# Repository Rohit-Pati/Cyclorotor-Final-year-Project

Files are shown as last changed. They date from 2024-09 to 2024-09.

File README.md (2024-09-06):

## Cyclorotor

Cyclorotor, also known as cycloidal rotor or cyclogiro, is a type of propulsion system which converts shaft power into the acceleration of fluid using a rotating axis parallel to the blade span (alternatively, rotating axis perpendicular to the direction of fluid motion). It consists of several blades around the axis of rotation with spanwise axis parallel to the axis of rotation. These blades are cyclically pitched twice per revolution implementing the control mechanism of Voith Schneider propeller to produce thrust in any direction normal to the axis of rotation.

This project was developed as part of the requirements for a bachelor's degree with the objective of experimentally observing the thrust pattern. A well-functioning four blades cyclorotor was manufactured using design parameters inferred and derived from various published articles.

## Design Specifications

Airfoil                                      : NACA0015

Chord Length                                 : 50.8 mm

Blade Span                                   : 171 mm

Blade distance offset from axis of rotation  : 3 inch (152.4 mm)

Pitching axis point                          : 25% of chord from leading edge

Control(actuation) point in airfoil          : 17.5 mm

Length of control rods                       : 76.2 mm

## Power System Specifications

Motor Specification  : 1400 KV

Driver Pulley        : GT2 Timing Pulley 20 Teeth with 5 mm bore

Driven Pulley        : GT2 Timing Pulley 60 Teeth

Pulley Belt          : GT2 Timing Pulley 200mm

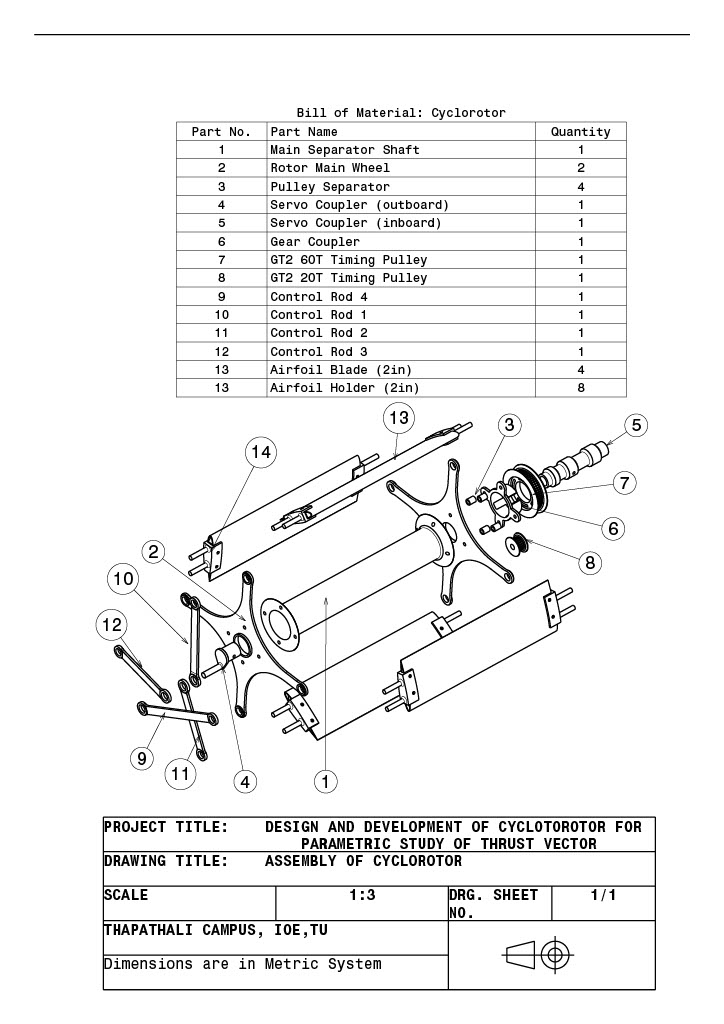
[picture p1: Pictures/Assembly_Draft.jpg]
Assembly


Here are some pictures of final product after manufacture and assembly.

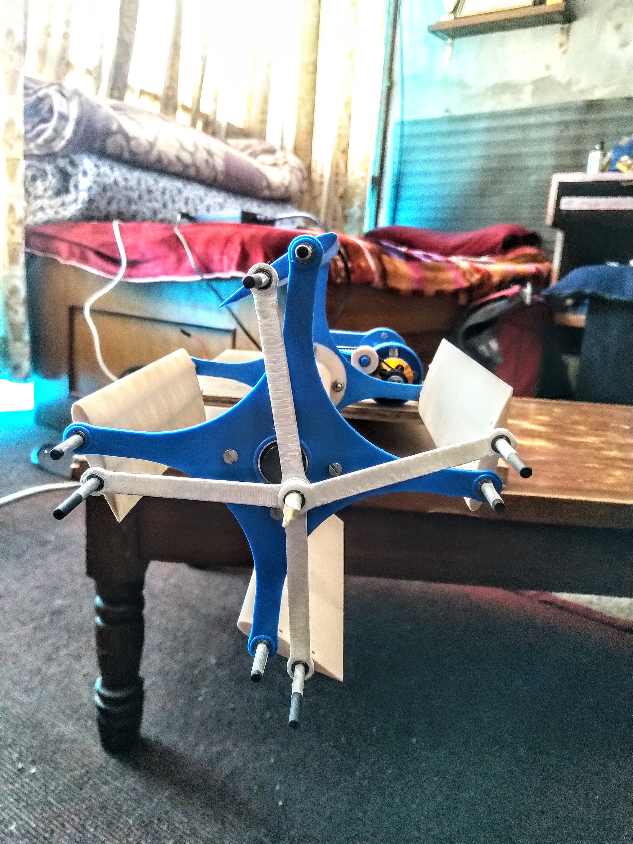
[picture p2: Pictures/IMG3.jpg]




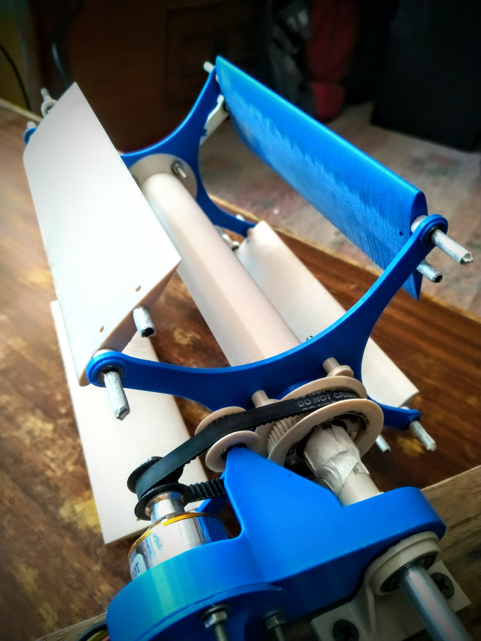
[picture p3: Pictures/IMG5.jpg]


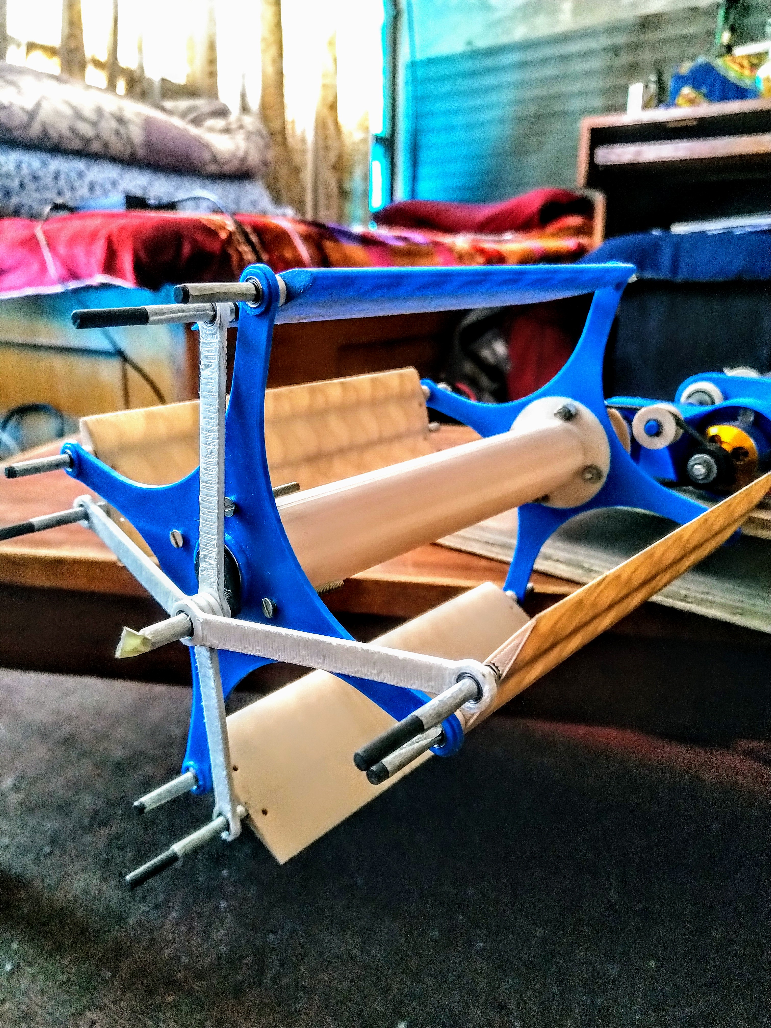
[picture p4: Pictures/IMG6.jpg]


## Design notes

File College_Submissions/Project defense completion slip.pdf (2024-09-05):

Department of Automobile and Mechanical Engineering FYP REPORT NO: 010

Batch: 2075 | Program: Bachelor’s in mechanical engineering (BME)

Final Year Title: DESIGN AND DEVELOPMENT OF CYCLOROTOR FOR PARAMETRIC

STUDY OF THRUST VECTORING

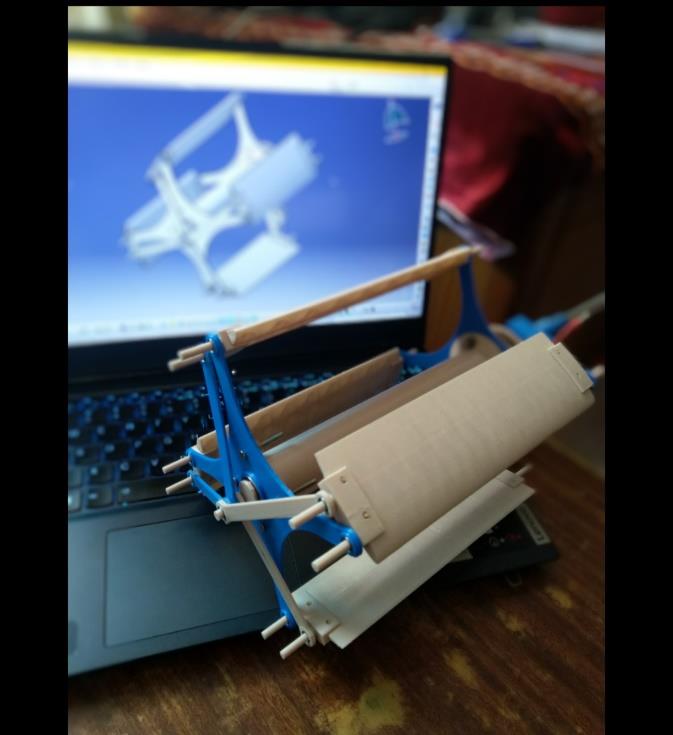
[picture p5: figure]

Student Name list/CRN:

Abhishek Kandel (THA075BME003)

Milan Dhami (THA075BME019)

Ringjing Tamang (THA075BME030)

Rohit Pati | (THA075BME031)

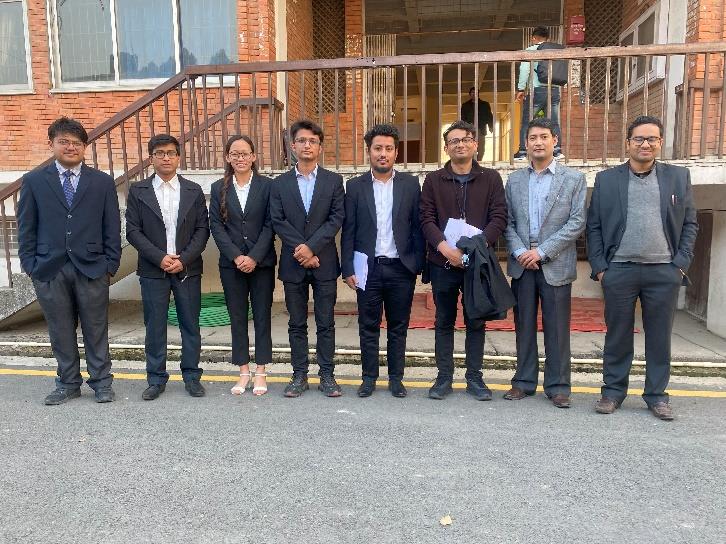
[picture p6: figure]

Contact:

abhisekrishi123@gmail.com

milandhami004@gmail.com

tamangrj22@gmail.com

rohit.075bme031@tcioe.edu.np

Supervisor:

Er.Biman Rimal

Abstract:

Cyclorotor is a horizontal axis propulsion system with airfoil blades attached between two rotor wheels parallelly to the axis of rotation. The unique feature of this propulsion system is the variable pitching mechanism which offers better maneuverability characteristic for air vehicles. This propulsion system is claimed to produce adequate thrust even at low speed which helps to simplify the rotating mechanism and reduce noise which has widened its scope for use in VTOL aircraft. Research has been going on in this field with the quest of optimizing it for use in air vehicles. It is important to have a better control system for propulsion systems and aircraft to acquire airworthiness. For a better control system of the variable pitching mechanism in a cyclorotor, it is required to have knowledge on the thrust vector pattern. Hence this report discusses the experimental study of thrust vector in cyclorotor where the thrust vector pattern is analyzed with respect to the eccentricity phase angle.

Department of Automobile and Mechanical Engineering FYP REPORT NO: 010

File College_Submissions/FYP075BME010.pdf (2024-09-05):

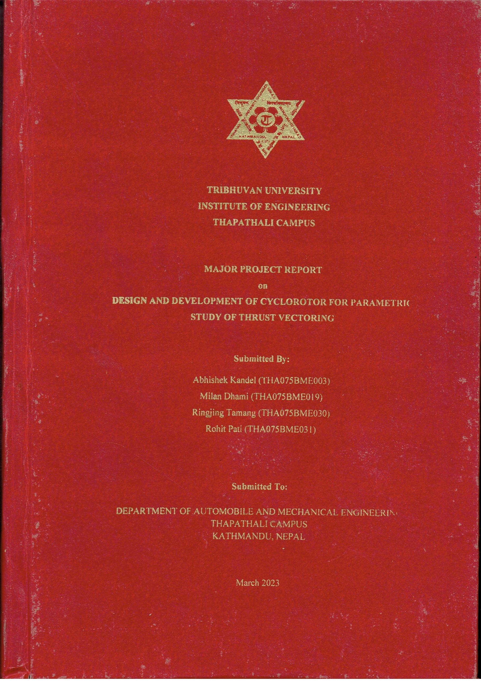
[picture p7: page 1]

TRIBHUVAN UNIVERSITY

INSTITUTE OF ENGINEERING

THAPATHALI CAMPUS

MAJOR PROJECT REPORT

on

DESIGN AND DEVELOPMENT OF CYCLOROTOR FOR PARAMETRIC

STUDY OF THRUST VECTORING

Submitted By:

Abhishek Kandel (THA075BME003)

Milan Dhami (THA075BME019)

Ringjing Tamang (THA075BME030)

Rohit Pati (THA075BME031)

Submitted To:

DEPARTMENT OF AUTOMOBILE AND MECHANICAL ENGINEERING THAPATHALI CAMPUS
KATHMANDU, NEPAL

March 2023

TRIBHUVAN UNIVERSITY

INSTITUTE OF ENGINEERING

THAPATHALI CAMPUS

MAJOR PROJECT REPORT

on

DESIGN AND DEVELOPMENT OF CYCLOROTOR FOR PARAMETRIC

STUDY OF THRUST VECTORING

Submitted By:

Abhishek Kandel (THA075BME003)

Milan Dhami (THA075BME019)

Ringjing Tamang (THA075BME030)

Rohit Pati (THA075BME031)

Submitted To:

DEPARTMENT OF AUTOMOBILE AND MECHANICAL ENGINEERING THAPATHALI CAMPUS, KATHMANDU, NEPAL

In the partial fulfillment of the award of the Bachelor’s Degree in Mechanical

Engineering

Under the Supervision of

Er. Biman Rimal

March 2023

ii

COPYRIGHT

The author has agreed that the library, Department of Automobile and Mechanical

Engineering, Thapathali Campus, Institute of Engineering may make this project report

freely available for inspection and study. Moreover, the author has agreed that

permission for extensive copying of this project report for scholarly purposes may be

granted by the professor who supervised the project work recorded herein or, in their

absence, by the Head of the Department wherein the project report was done. It is

understood that recognition will be given to the author of this report and to the

Department of Automobile and Mechanical Engineering, Thapathali Campus, Institute

of Engineering, in any use of the material of this project report.

Copying or publication or other illegal and immoral use of this report for financial gain

without the approval of the Department of Automobile and Mechanical Engineering,

Thapathali Campus Institute of Engineering and author’s written permission is strictly

prohibited.

Request for permission to copy or to make any other use of the material in this report,

in whole or in part, should be addressed to:

Head

Department of Automobile and Mechanical Engineering

Thapathali Campus, Institute of Engineering

Thapathali, Kathmandu

Nepal

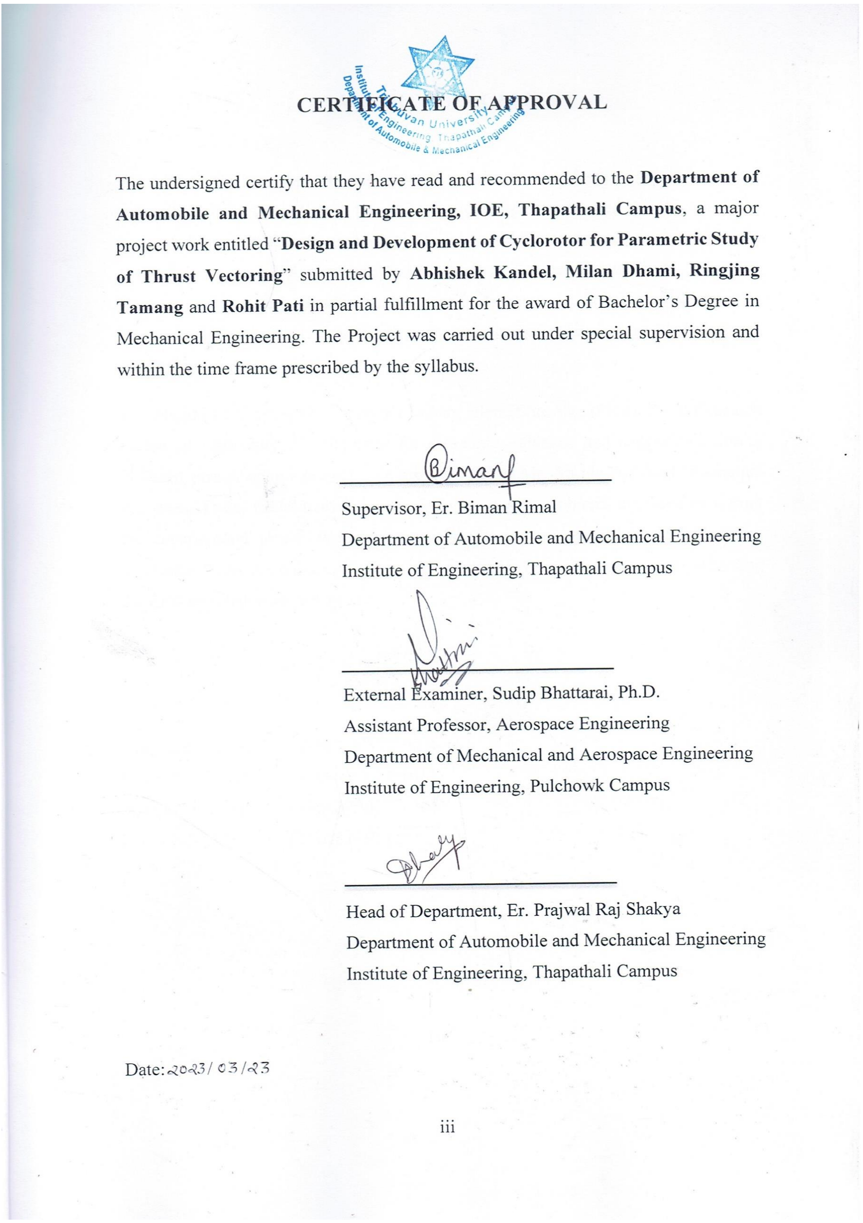
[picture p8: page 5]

iii

CERTIFICATE OF APPROVAL

The undersigned certify that they have read and recommended to the Department of

Automobile and Mechanical Engineering, IOE, Thapathali Campus, a major

project work entitled “Design and Development of Cyclorotor for Parametric Study

of Thrust Vectoring” submitted by Abhishek Kandel, Milan Dhami, Ringjing

Tamang and Rohit Pati in partial fulfillment for the award of Bachelor’s Degree in

Mechanical Engineering. The Project was carried out under special supervision and

within the time frame prescribed by the syllabus.

Supervisor, Er. Biman Rimal

Department of Automobile and Mechanical Engineering

Institute of Engineering, Thapathali Campus

External Examiner, Sudip Bhattarai, Ph.D.

Assistant Professor, Aerospace Engineering

Department of Mechanical and Aerospace Engineering

Institute of Engineering, Pulchowk Campus

Head of Department, Er. Prajwal Raj Shakya

Department of Automobile and Mechanical Engineering

Institute of Engineering, Thapathali Campus

Date: yyyy/mm/dd

iv

ACKNOWLEDGEMENT

We would like to take this opportunity to express the deepest gratitude to our

supervisor, Er. Biman Rimal for offering immense support and guidance for the

successful accomplishment of this project. We would like to extend our sincere thanks

to the Department of Automobile and Mechanical Engineering and IOE Thapathali

Campus for providing us with the opportunity to conduct this project. We are also

thankful to all the lecturers and faculty who have helped us directly and indirectly on

this project.

We would like to extend our gratitude to Mrs. Elena Shrestha, (Postdoctoral Research

Fellow at University of Michigan) for providing guidance and suggestions during

different phases of our project. We are thankful to Mr. Moble Benedict (Associate

Professor, Texas A&M University) for helping us with problems encountered during

the experimental phase. We would also like to extend our thanks to Mr. Julian

Schliessus (MSc Aerospace, University of Stuttgart) for providing support regarding

the CFD simulation on this project.

Abhishek Kandel | (THA075BME003)
Milan Dhami | (THA075BME019)
Ringjing Tamang | (THA075BME030)
Rohit Pati | (THA075BME031)

v

ABSTRACT

Cyclorotor is a horizontal axis propulsion system with airfoil blades attached between

two rotor wheels parallelly to the axis of rotation. The unique feature of this propulsion

system is the variable pitching mechanism which offers better maneuverability

characteristic for air vehicles. This propulsion system is claimed to produce adequate

thrust even at low speed which helps to simplify the rotating mechanism and reduce

noise which has widened its scope for use in VTOL aircraft. Research has been going

on in this field with the quest of optimizing it for use in air vehicles. It is important to

have a better control system for propulsion systems and aircraft to acquire

airworthiness. For a better control system of the variable pitching mechanism in a

cyclorotor, it is required to have knowledge on the thrust vector pattern. Hence this

report discusses the experimental study of thrust vector in cyclorotor where the thrust

vector pattern is analyzed with respect to the eccentricity phase angle.

vi

TABLE OF CONTENTS

COPYRIGHT | ii
CERTIFICATE OF APPROVAL | iii
ACKNOWLEDGEMENT | iv
ABSTRACT | v
TABLE OF CONTENTS | vi
LIST OF FIGURES | xi
LIST OF TABLES | xv
LIST OF ABBREVIATIONS | xvi
CHAPTER ONE: INTRODUCTION | 1
1.1 | BACKGROUND | 1
1.2 | INTRODUCTION | 4
1.3 | PROBLEM STATEMENT | 5
1.4 | PROJECT OBJECTIVES | 6
1.4.1 | MAIN OBJECTIVE | 6
1.4.2 | SPECIFIC OBJECTIVES | 6
1.5 | SCOPES OF CYCLOROTOR | 6
CHAPTER TWO: LITERATURE REVIEW | 8
CHAPTER THREE: METHODOLOGY | 17
3.1 | REVIEW OF LITERATURES | 17

vii

3.2 | OBSERVATION | 17
3.3 | SOFTWARES EMPLOYED | 17
3.3.1 | CATIA V5 | 17
3.3.2 | XFLR5 | 18
3.3.3 | OpenFOAM | 18
3.4 | PROJECT FLOW CHART | 20
CHAPTER FOUR: MATHEMATICAL MODELING | 21
4.1 | AIRFOIL MODELING | 21
4.2 | CYCLOROTOR | 23
4.2.1 | KINEMATIC MODEL | 24
4.2.2 | AERODYNAMIC ANALYSIS | 26
4.3 | TRANSMISSION GEAR AND BELT | 29
4.3.1 | GT2 TIMING PULLEY | 29
4.3.2 | GT2 TIMING BELT | 30
4.4 | LOAD CELL | 31
CHAPTER FIVE: MATERIALS AND COMPONENTS SELECTION | 32
5.1 | MATERIALS FOR FABRICATION | 32
5.1.1 | PLA FILAMENT | 32
5.1.2 | ALUMINUM TUBE | 33
5.1.3 | CARBON FIBER ROD | 34
5.2 | COMPONENTS | 35

viii

5.2.1 | GT2 TIMING BELT | 35
5.2.2 | 1400 KV BRUSHLESS DC (BLDC) MOTOR | 35
5.2.3 | ELECTRONIC SPEED CONTROLLER (ESC) | 36
5.2.4 | LITHIUM POLYMER BATTERY | 37
5.2.5 | SERVO TESTER | 38
5.2.6 | STEEL BOLTS AND NUTS | 38
5.2.7 | STEEL MACHINE SCREWS | 39
5.2.8 | LOAD CELL | 40
5.2.9 | HX711 MODULE | 41
5.2.10 | ARDUINO UNO | 41
CHAPTER SIX: DESIGN, SIMULAITON AND ANALYSIS | 43
6.1 | AIRFOIL DESIGN AND ANALYSIS | 43
6.2 | ROTOR DESIGN | 45
6.2.1 | ROTOR WHEEL | 46
6.2.2 | AIRFOIL BLADE | 48
6.3 | TRANSMISSION DESIGN | 51
6.3.1 | GEAR DESIGN | 51
6.3.2 | BELT DESIGN | 52
6.4 | SIMULATION OF CYCLOROTOR | 52
6.4.1 | SOLVERS | 52
6.4.2 | TURBULENCE MODELING | 54

ix

6.4.3 | THE SST K-ω TURBULENCE MODEL | 55
6.4.4 | ARBITRARY MESH INTERFACE (AMI) | 55
6.4.5 | MESHING | 55
6.4.6 | BOUNDARY CONDITIONS: | 58
6.4.7 | MOTION OF BLADES | 60
6.4.8 | SIMULATION | 60
6.4.9 | POST PROCESSING: | 61
CHAPTER SEVEN: MANUFACTURING AND ASSEMBLY | 65
7.1 | FABRICATION | 65
7.1.1 | CYCLOROTOR | 65
7.1.1.1 | MAIN ROTOR WHEEL | 65
7.1.1.2 | AIRFOIL BLADE | 65
7.1.1.3 | CARBON ROD SPAR | 66
7.1.1.4 | CONTROL ROD | 66
7.1.1.5 | MAIN ROTOR SEPARATOR SHAFT | 67
7.1.1.6 | SERVO-SHAFT COUPLER | 68
7.1.1.7 | PULLEY COUPLER | 69
7.1.1.8 | TIMING PULLEY | 69
7.1.2 | TEST RIG | 70
7.2 | ASSEMBLY | 72
7.2.1 | CYCLOROTOR | 72

x

7.2.2 | EXPERIMENTAL SETUP | 73
CHAPTER EIGHT: EXPERIMENTATION, RESULT AND DISCUSSION | 75
8.1 | EXPERIMENTATION | 75
8.2 | EXPERIMENTAL RESULTS AND DISCUSSION | 77
CHAPTER NINE: CONCLUSION | 82
CHAPTER TEN: PROBLEMS AND LIMITATIONS | 83
10.1 | PROBLEMS | 83
10.2 | LIMITATIONS OF THE PROJECT | 83
REFERENCES | 84
APPENDICES | 88

xi

LIST OF FIGURES

Figure 10 Horizontal and vertical resultant force components of blade in hovering state

xii

xiii

Figure 51 Coordinate system for the whole system (left) coordinate system for phase

xiv

Figure 61 Shear Force Diagram | 88
Figure 62 Bending Moment Diagram | 89

xv

LIST OF TABLES

Table | 5 | GT2 | Timing | Belt | Specification | (Source:

Table 6 Carbon Fiber Properties (Source: https://goodwinds.com/technical-material-

xvi

LIST OF ABBREVIATIONS

2D | Two Dimensional
BLDC | Brushless Direct Current
CBS | Cycloidal Blades System
CFD | Computational Fluid Dynamics
ESC | Electronic Speed Controller
FM | Figure of Merit
GA | Genetic Algorithm
GM | Gradient Method
IAT | Innovation Aeronautics Technologies
MAV | Micro Air Vehicle
PIV | Particle Image Velocimetry
PLA | Polylactic Acid
SOGA | Single-Objective Genetic Algorithm
URANS | Unsteady Reynold-Averaged Navier Stokes
VTOL | Vertical Take Off Landing
mph | miles per hour
PIMPLE | Pressure Implicit Method for Pressure-Linked Equations

1

### 1 CHAPTER ONE

INTRODUCTION

### 1.1 BACKGROUND

Ideas regarding cyclorotor were present even during the 19th century. In 1909 Russian

engineer Sverchkov proposed "Samoljot", also named - "wheel orthopter" which even

though is difficult to classify as cyclocopter can be regarded as a proto-cyclocopter. It

used 3 flat surfaces and rudder and lift and thrust had to be generated by paddle wheels.

It was unsuccessful and couldn’t fly (Bowers, 2013).

In Feb 1923, Jonathan Edward Caldwell from US filed an application for a patent

covering a “Cyclogyro” that was designed to take off vertically and transit to forward

flight. The plane's wings were small airfoil blades mounted in Ferris wheel-like rotating

frames protruding from either side of a conventional aircraft fuselage. The “Cyclogyro”

patent was granted in the summer of 1927. But this device was too unstable for human

flight (Jonathan Edward Caldwell - Wikipedia, 2022).

Figure 1 Sverchkov's Samoljot, St-Peterburg, 1909 (Bowers, 2013)

In 1933, experiments in Germany by Adolf Rohrbach resulted in a paddle-wheel wing

arrangement. Oscillating winglets went from positive to negative angles of attack

during each revolution to create lift, and their eccentric mounting would, in theory,

produce nearly any combination of horizontal and vertical (Arndt, n.d.) forces but the

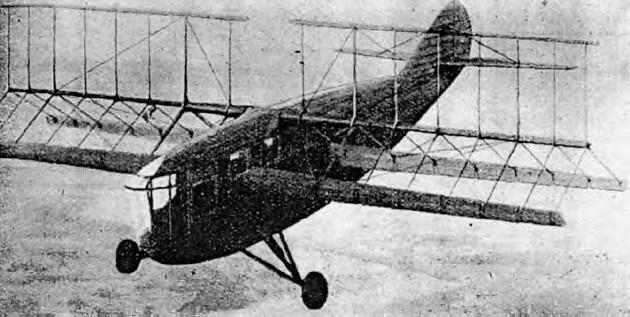
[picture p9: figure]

2

foreign aviation journals of the time casted doubt on the soundness of the design which

meant that funding for the project could not be raised.

Figure 2 Rohrbach Cyclogyro (Arndt, n.d.)

Also, in 1933 NACA Technical Memorandum No. 727, C. B. Standgren claimed that

his pioneer paper to be made public described the theory behind the cyclogyro in any

real technical detail. Standgren’s analysis described the kinematics of blade movement

for a cycloidal rotor. His observations were derived from “numerous tests made at the

Institut Aerotechnique de Saint-Cyr, by means of different small-scale models

constructed with the cooperation of the Office National de Inventions et de la Societe

‘’Expansion Franco-Scandinave’ relations.” He also states that the Liore and Oliver

airplane company built a full-scale aircraft. There was no discussion of the actual tests

rather Standgren mathematically described the kinematics of the cycloidal rotor and the

mechanism by which generated thrust (Strandgren, 1933). In the same year an

experimental model of the cyclogyro was first presented by John B. Wheatley

(Wheatley, Rotating-wing Aircraft Compared to Conventional Airplanes, 1934). In

1934, he and Ray Windley tested a rotor with 4 blades of chord 0.312 ft, and a diameter

and wingspan of 8ft. The experiment results showed that the cyclogyro of these

dimensions “would be able to ascend vertically, fly horizontally, and glide without

power” (Wheatley, Choice of Airfoils for Rotating Wing Aircraft, 1934).

3

The main problems faced by models until now was the requirement of high strength

material. Though the first successful flight was possible by the 1930s it was too unstable

and unsafe. Research on the subject was mostly abandoned after World War II, with

researchers unable to design a control mechanism suitable for the aircraft, and rotor

propeller becoming used for vertical take-off dominantly. The biggest issue in

cyclorotors was the fact that blades must take large transverse centrifugal bending

loads, and during that time, they did not have the materials that had the strength-to-

weight ratio to do that. But modern technology and the use of computational fluid

dynamics in vehicle design along with material advancement has made practical

prototype development possible.

Even though many attempts were made to build such an aircraft and numerous patents

were filed, successful flight of a cycloidal rotor aircraft remained as an impossible feat

for nearly a century, until recently when the first cyclocopter was flown at the

University of Maryland in 2011 by team of Mobile Benedict and R.Gupta (Jarugumilli,

Chopra, & Benedict, 2011) (Benedict, Chopra, & Gupta, Design, Development and

Open-Loop Flight-Testig of a Twin-Rotot Cyclocopter, 2013). And further feasibility

of this concept was demonstrated here again in 2013 with a quadrotor cyclocopter

capable of free hover by Mobile Benedict, Joseph Mullins, and Vikram Hrishikeshavan.

This quadrotor had a gross weight of 800 grams and 2 ft by 2 ft by 1.5 ft in dimension

(Benedict, Joseph, Chopra, & Gupta, 2016). An untethered model cyclocopter was

flown in 2011 at the Northwestern Polytechnic Institute in China.

On the 20th of August 2021, Cyclotech, an Austrian company made a cyclorotor that

performed its first free flight and landing with the Cyclorotor technology (CycloTech

Home - CycloTech Reovlution of motion, 2021).

Advanced Research Foundation (ARF), the research arm of the Russian Military, is

also working on a cyclorotor. ARF concluded after year-long research that the best

iteration for a flying vehicle that can carry a load of 220 - 2,200 pounds with passengers

is a cyclocopter (Blain, 2021).

4

### 1.2 INTRODUCTION

A cyclorotor (cyclogyro, cyclocopter, cycloidal propeller) is a heavier-than-air flight

vehicle capable of vertical takeoff and landing using cyclically pitched, horizontal rotor

blades. Typical configurations consist of 4 to 6 rotor blades per rotor, which spin

parallel to each other around a central axis. As they turn, the rotor blades pivot about

their longitudinal axis. The pivot function is periodic, with each rotation about the

common axis defining the frequency of the pitching function. Pivot functions resemble

a sine curve and function to generate a constant lift, keeping a positive angle of attack

in quadrants one and two, and a negative angle of attack in quadrants three and four.

However, the pivot functions can be adapted to be more efficient in different flight

envelopes, for example during hovering, forward flight, or maneuvering. A key

characteristic of a cyclorotor is that it can very rapidly change its pivot function, almost

instantly changing direction and magnitude of thrust. Magnitude of thrust is altered by

changing the amplitude of the pivot function, and the direction of thrust is changed by

shifting the phase of the pivot function. Cycloidal rotors are a viable means to produce

aerodynamic forces whose direction can be rapidly varied 360◦ in a plane normal to the

axis of rotation. The superposition of two blade motions generates the thrust. For one

motion, the blades rotate about the rotor center while maintaining their span axes

always parallel to the axis of the central drum. For the other motion, the blades

individually pitch about their own pivoting axis with the same frequency as the main

rotation. Changing the phase delay or the magnitude of their pitching motion allows

almost instant thrust direction adjustments. The most frequent means to impose the

pitching motion to the blades is with rigid links. The central offset of these links

generates the cyclic pitching motion of the blades.

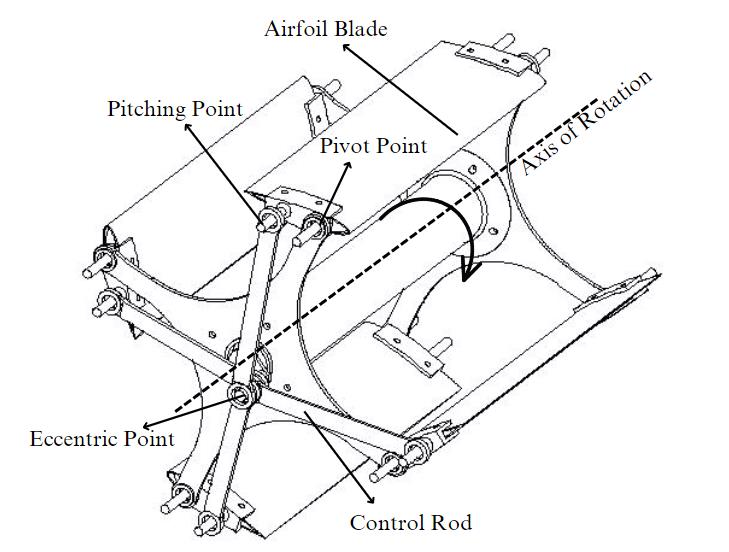
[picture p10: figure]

5

Figure 3 Cyclorotor model

### 1.3 PROBLEM STATEMENT

Concept of cyclorotor dates to the time when different innovations and experiments on

aviation were carried out before airplanes and helicopters were fully realized; however

due to low strength to weight ratio materials this concept was considered unviable. With

the advent of time and development of high strength to weight ratio materials this

concept has been brought back to research. Research has been carried out on control

mechanisms, optimization of the mechanism and its feasibility to be used on aircraft

propulsion. Different optimization techniques and different analysis methods had been

used to model the best performing cyclorotor. Besides the efforts being made it has

been very hard for the researchers to gain stable and controlled flight with this

propulsion system. The cyclorotor features a variable pitching mechanism which allows

the blades to pitch while it is rotating about the central rotational axis. This unique

feature of the cyclorotor enables thrust vectoring which can aid the aircraft to gain better

6

maneuverability. Besides the fact that the thrust vectoring analytical model plays a

significant role in flight performance of the cyclorotor, more research has been carried

out on other than this specific portion of the cyclorotor. Therefore, we intend to develop

a cyclorotor model and conduct a parametric study on it with an objective to obtain the

thrust vectoring patterns with respect to the eccentricity phase angle which is the sole

responsible parameter for the thrust vectoring.

### 1.4 PROJECT OBJECTIVES

The main object of this project is to experimentally study the thrust vector pattern

generated due to the variation in eccentricity phase angle.

### 1.4.1 MAIN OBJECTIVE

- To design, build and study the thrust vectoring pattern in cyclorotor.

### 1.4.2 SPECIFIC OBJECTIVES

- To design and build a cyclorotor.
- To design and fabricate a thrust test rig.
- To conduct an experimental study on thrust vectoring pattern in cyclorotor.

### 1.5 SCOPES OF CYCLOROTOR

When compared to a conventional edgewise rotor at the same disk loading (thrust/disk

area), an optimized cyclorotor has a higher power loading (thrust/power) in hover.

Since all spanwise blade sections of the cyclorotor operate under similar aerodynamic

conditions, the blades can be optimized to achieve best aerodynamic efficiency. In

addition, the uniform spanwise distribution of aerodynamic forces enables the

cyclorotor to operate at lower tip speeds, thereby improving the acoustics signature.

Previous PIV studies have also shown the existence of beneficial unsteady aero-

dynamic mechanisms, such as leading-edge vortices that delay the onset of blade stall

and improve the lift producing capability and aerodynamic efficiency of the cyclorotor

(Leger, Pascoa, & Xisto, 2015).

7

Another advantage of the cyclorotor is its unique thrust vectoring capability that is

achieved by varying the phase of the cyclic pitching. By thrust vectoring instead of

pitching the vehicle forward, the cyclocopter can achieve level forward flight in a

power-efficient manner. Previous wind tunnel studies on an isolated cyclorotor found

that thrust vectoring enables a cyclocopter to potentially reach up to 13 m/s (29 mph)

without relying on additional lift augmenting devices/surfaces. It was observed that the

power required for a cyclorotor to maintain a steady, level flight significantly drops

with forward speed, up to almost an advance ratio of 1.0, due to increased lift producing

efficiency of the cyclorotor (Jarugumilli, Chopra, & Benedict, 2011). Thrust vectoring

also improves maneuverability and capability of operation in gusty environments.

8

### 2 CHAPTER TWO

LITERATURE REVIEW

(Lee, Jung, & Hwang, 2004) carried out research on cycloidal blade system and

cyclocopter in 2004, in which an analytical model was developed by using momentum

theory and Blade element theory to examine the characteristic and performance of

cyclocopter and to predict the thrust and power. Assuming the cycloidal blade system

can be represented by a pair of actuator disks in tandem, the momentum theory and

blade element theory was applied to the upstream half and downstream half of the rotor

and induced velocity and thrust produced was calculated. The induced flow speed as a

function of azimuth angle was observed in which the inflow speed was zero at azimuth

angle 0º and 180º. Also, the flow speed increased with increased azimuth angle up to

90º and after this flow passed slowly. The flow pattern was symmetric about the vertical

axis in the upstream but axisymmetric of the flow through the downstream rotor was

lost because in the downstream total flow through the rotor flight path was composed

of the component of the equilibrium of induced velocities. The induced flow in the

region 180º < ψ < 270º in the downstream half of the rotor was entering the rotor while

in 270º < ψ < 360º the flow was leaving the rotor. The magnitude of the flow velocity

in the downstream rotor was smaller than that in the upstream. The lift coefficient

variations with respect to blade azimuth angle was examined for a blade having chord

to radius ratio (c/R) = 0.375 with camber effect or without camber effect. And it was

found that the lift coefficient shifted downward by approximately 0.5 compared to that

without camber effect. Whereas the vertical force component decreased in the upstream

part but increased in the downstream part for a blade with camber effect. The

aerodynamic forces and moment for the rotor span was calculated by integrating along

the blade from the root to the tip. The total thrust produced on a rotor by all the blades

was obtained by the resultant of all vertical forces and horizontal forces obtained from

the resolution of the radial and tangential forces. Considering all profile drag and

induced drag torque was calculated and thus the power required to turn the blades was

obtained. The moving mesh method was used in CFD analysis to determine the

aerodynamic design parameter and understand the flow conditions around rotor and

blades. To improve the accuracy of CFD, Cycloidal Blade System (CBS) test apparatus

9

was generated, and results were compared. It was found that CFD analysis can predict

the thrust of the CBS rotor as well. The experiments showed that the cycloidal rotor can

produce thrust in any direction in the rotation plane and the rotor has hovering

capability as well as forward flight capability.

From the experiment done after the development of the cycloidal blade system by

implementing a sinusoidal low pitch system to investigate the fundamental

characteristics in hovering state it was found that, with increase in rotating speed, pitch

angle, rotor radius and number of blades, the thrust also increased. Whereas the

efficiency decreased with increased number of blades as profile drag also increased and

efficiency increased with increased rotor radius as it resulted in decreased solidity.

Power increased rapidly as the rotating speed was increased in proportion to the cube

of the rotating speed. Maximum thrust was generated at a pitch angle of 30º due to

power limitation. Compared with hovering efficiency of other aircrafts it was found

that cyclocopter had hovering efficiency higher than other aircrafts. They concluded

that maximum hovering performance could be obtained at low rotating speed resulting

in better efficiency and at low thrust level.

They designed a cyclocopter of 43kg including 7kg payloads and rotor torque was

compensated by locating the center of gravity 50cm below in vertical direction and the

34 cm after in the horizontal direction from the rotor axis. They concluded that the

cycloidal blades system can be used as a powerful thrust system capable of easy thrust

vectoring, and the efficiencies for the aircraft with cycloidal rotor may compare

favorably with values for other vertical takeoff and landing aircraft.

In 2005, (YUN, PARK, HWANG, & KIM, 2005) studied the mathematical modeling

of thrust control mechanism of VTOL UAV and cyclocopter. They used sinusoidal low

pitch system in which the control forces can be divided into the control force for

magnitude of thrust (component in the direction of line joining center of the rotor and

point of eccentricity) and the control force for direction of thrust (component

perpendicular to the direction of line joining center of the rotor and point of

eccentricity). The control of thrust direction was done by rotating mechanism and was

calculated by formulating a numerical modeling to calculate the control thrust. It was

found that when a control rod was located at the upper side of the CBS rotor, the load

10

applied to the control rod was compressible. Reversely, when a control rod was located

at the lower side of the CBS rotor, the control rod was under tension loading state. The

applied control force at the eccentricity points in the longitudinal direction over the

range of 0º < Ψ < 90º. Maximum force occurred at about Ψ = 0º and Ψ = 90º. They

concluded that the control of magnitude and direction of thrust can be done by a control

block motion in a translation manner and the servo motors and servo linkages system

must be selected and designed to be operated under the action of control force and

torque.

In 2013, (Benedict, Jarugumilli, & Chopra, Effect of Rotor Geometry and Blade

Kinematics on Cycloidal Rotor Hover Performance, 2013) investigated the effects of

rotor geometry and blade kinematics on performance of the cyclorotor in terms of both

thrust and power loading (thrust/power). They built a test setup with a load cell to

measure the thrust, torque, and rotational speed of the cyclorotor. The baseline rotor

they tested had a rotor diameter of 6-inch, blade span of 6.25-inch and chord length of

1.33-inch. The airfoil used was the NACA0015 and a hall effect sensor was used to

measure the rotational speed. They studied the virtual camber effect and found that

asymmetric blade pitching, and the pitching axis location can affect the performance of

a cyclorotor. They varied the different parameters and studied the effects of the

parameters on the performance of the rotor which include the rotor radius, blade span,

chord, and blade planform. Radii of the rotor tested include 2, 3, 4, and 5 inches. Blade

spans varied as 3.75, 4.69, 6.25 and 9.38 inches. Blade chords varied as 0.665, 0.887,

1.33, 1.665, 2 and 2.5 inch. The blade pitching amplitude of the rotor investigated includes 25o

, 35o

, 40o

, and 45o with the rotational speeds ranging from 400 to1800

RPM. On experimenting they observed that thrust and power does not vary much with

radius, however thrust increased with increasing chord for constant blade speed. They

concluded the power loading of the cyclorotor would vary significantly with radius for

a constant chord. In contrast, their experiment showed that the power loading to disk

loading was higher for a smaller rotor radius (2 inch for this case) keeping the chord

constant. The experiment also concluded that power loading is identical if the

chord/radius ratios are same even if the radii of the rotors are different. The chord/radius ratio of 0.835 yielded the best power loading with pitching angles of 40o
and 1800

RPM. Power loading decreased drastically for chord/radius ratio more than 0.83. They

11

also concluded that the optimum chord/radius ratio is 0.8 and 0.5 for 40o

and 20o

pitching amplitude respectively.

Experiments carried with different blade spans with rotor radius 3 inch and chord 1.33

inch showed that thrust producing capability decreases linearly with blade span at

constant speed. The article also states that the rotors with shorter span performed slightly better at higher disk loading for 40o
pitching amplitude, the reason being not

understood at that point. Another key conclusion made was, for a constant disk loading,

the maximum power loading not only depends on the optimum chord/radius ratio but

also on the total blade area of the rotor.

From the experiment carried out on the solidity, Benedict and associate researchers

suggested that if solidity of the cyclorotor needs to be increased, the better approach is

to increase the blade chord rather than increasing the number of blades using a smaller

blade chord.

Benedict and his associates experimented on symmetric and asymmetric pitching

either. For the symmetric pitching test, they used a 3-inch radius rotor, blades with 2-

inch chord and 6.25-inch span as this was the optimum geometry obtained from their

former experiments. They observed that increasing thrust by increasing the blade

section angle of attack seemed more efficient than increasing the rotation speed. They

concluded that maximum thrust which can be obtained by using this approach would

still be limited by the onset of blade stall, and hence will be airfoil dependent since at

low Reynolds numbers the profile drag coefficient is sensitive to the blade section angle

of attack even before stall. For asymmetric pitching, the best power loading was

obtained when the blades operated at a higher pitch angle at the top and a lower pitch

angle at the bottom and the optimum blade kinematics was provided by pitch amplitude of 45o

at top and 25o
at bottom.

(Hrishikeshavan, Benedict, & Chopra, 2014) in 2014 in continuation to their research

and experiment on the cyclorotor, performed another research and experiment on

identification of flight dynamics of cyclocopter MAV in hover. For this purpose, they

built an optimal performance cyclorotor with blade area/rotor area ratio of 0.35 and blade chord/radius ratio of 0.625. The maximum blade pitch angle of 45o was used and

the airfoil used was NACA0015. They tested the flight dynamics where they

12

implemented the feedback control system to control the roll, yaw, and pitch of the

cyclocopter. Their cyclocopter was controlled by an on board MSP430 microprocessor

which worked in coordination with ITG3200 triaxial gyros, KXSD9 triaxial

accelerometer and 2.4 GHz ATMEL transceiver. The attitude of the cyclocopter was

as; pitch was controlled by controlling the speed of tail rotor, roll and yaw was

controlled by controlling or providing differential speed to the cyclorotor. An important

observation was that the roll and yaw degrees of freedom were tightly coupled due to

gyroscopic effects.

As their primary objective they worked on the flight dynamics identification and

analysis of maneuverability and gust disturbance rejection potential of a vertical takeoff

and landing capable cycloidal rotor MAV. They performed systematic input excitation

tests along all degrees of freedom in the closed-loop condition in hover, extracted the

flight dynamics model using time-domain system identification techniques based on

input and output data. It was found that the longitudinal and heave degrees of freedom

were decoupled from the rest of the dynamics, whereas the lateral and yaw modes were

highly coupled due to the gyroscopic effect.

(Hrishikeshavan, Benedict, & Chopra, 2014) continues their research focusing on

developing control strategies for twin cyclocopter in forward flight and conducting

wind tunnel testing. Here 550-gram vehicle was used with lateral dimension of 0.381

m, longitudinal dimension of 0.457 m and height 0.305 m with every cyclorotor having

diameter of 0.152 m, blade span of 0.171 m, chord length of 0.051 m being driven by

75 Watts motor. Each blade uses NACA0015 airfoil. The chord to radius ratio was

0.625. A closed loop feedback control system was used for stabilizing along with a

proportional derivative controller. Gyroscopic and control cross coupling is present

which increases mainly at higher phase angles due to the increase in magnitude of

propulsive forces there. So thrust vectoring has a larger impact on roll (left or right)

moments and change in rotor rotation has a large impact on yaw moment (clockwise or

counterclockwise). A positive roll(right) for the cyclorotor results in rotating speeds of

the left motor to increase and right motor to decrease. At higher phase angles this gives

a positive yaw(clockwise). So, this paper suggests that to get a pure roll controller

should give command for positive roll with negative yaw(counterclockwise) which

cancels yaw and negates effects of revolution per minute on yaw and results in pure roll

13

output. Similarly positive yaw with negative roll is needed to accomplish pure yaw

output as well. Tests also conclude that for constant phase angle varying forward

velocity does not significantly increase the coupling. According to the test the vehicle

successfully demonstrated steady level forward flight up to maximum of 5m/s forward

velocity and a satisfactory steady level forward flight was obtained with pitch and roll

angles held close to zero. The rate of transition from hover condition to forward flight

depends entirely on phase angle input. This paper also proves that when transitioning

from forward flight to hover, a cyclocopter can immediately stop even when moving at

an appreciable speed. At constant phase angle and forward velocity, increasing

rotational speed resulted in an increase of both lift and thrust consequently increasing

the power. However, increasing phase angle of the cyclorotor while keeping both

forward velocity and rotational speed constant resulted in increase in thrust and

decreased lift. Due to this this paper concludes that rotational speed and phase angle

should be controlled for steady level flight (thrust = drag, lift = weight).

This paper (Leger, Pascoa, & Xisto, 2015) first proposes and then discusses an

analytical or mathematical model to use during the design of cycloidal rotors. This uses

semi-empirical ways to derive the relations. To prove the relations three different rotor

configurations were used where rotor parameters like pitch amplitude, pitching axis

location, blade chord, airfoil thickness and phase angle of eccentricity were varied. This

model gave reliable estimation for thrust generated and power required operation of the

cycloidal rotor when compared with experimental data from Bosch Aerospace, Seoul

National university and IAT (Innovation Aeronautics Technologies) with deviation of

data for forces of just 4.8%, 1.6% and 12.8% respectively and deviation for power of

4.2%, 8% and 3.4% respectively which shows this model is reliable. The relation was

that thrust coefficient and power coefficient increase linearly with rotational velocity.

During construction of the rotor, it is important to know about the motion of blades due

to pitch mechanical control as it leads to non-perfect cycloid or to a pure cycloidal

motion which is important to know for aircraft control. This paper also shows us that

maximum pitch angle may be increased by increasing the magnitude of eccentricity.

Maximum and minimum values of angular velocity and acceleration are affected by

rotational speeds but the azimuthal angles where they occur are due to phase angle of

14

eccentricity phase angle. This model proposed by this paper is very important to define

the control in lift and thrust forces when operating a cyclorotor based air vehicle.

In this article (Shrestha, Yeo, Benedict, & Chopra, 2017) designs a 60-gram cycloidal

rotor for micro air vehicle tasks and analyzes which would be best design choices. To

design data from previous studies are used here as well. Micro air vehicles are those

aircraft with maximum dimension of 15 cm and maximum weight of 100 grams defined

by Defense Advanced Research Projects Agency (DARPA) in 1997 (McMichael & S.

Francis, 1997). The first objective here was to develop a lightweight cyclorotor. Most

weight will be in the cyclorotor with each rotor having four composite blades. Here two

cyclorotor with 60-gram weight are used. The cyclorotor uses NACA 0015 airfoil with

maximum pitching amplitude of 45 degrees which are milled out of carbon fiber and

evenly distributed along the span to maintain airfoil shape. This has minimum lateral

dimensions of 0.178 m, longitudinal dimensions of 0.127 m and height of 0.153 m with

diameter 0.076 m, blade span 0.043 m, chord of 0.022 m which are results from

previous experiments. The pitching axis here has a carbon fiber spar that is present

throughout the entire blade structure along with carbon fiber spar to provide a

connection to the blade pitching mechanism. Here foam leading edge and stringers are

used. This has managed to reduce the weight of the blade by 67% in comparison to

conventional design. Four 0.5-gram blades on a twin cyclocopter are the preferred

choice in this experiment. The chord to radius ratio is 0.57 and pitching axis location is

25% of blade chord. Tail rotor with 33 grams of thrust at 8000 rpm, closed loop

feedback system with proportional derivative controller for stabilization are other

features here. A horizontal tail rotor is used to counter the pitch down moment that

occurs due to both rotors rotating clockwise. This capacity of the tail is increased by

increasing the horizontal offset between this rotor and the vehicle's center of gravity

according to this paper. The pitch down moment also causes unbalanced angular

momentum and gyroscopic effect happens. Due to this, for a positive roll vehicle

responds in both rolls right and counterclockwise and for positive yaw (clockwise)

cyclocopter responds in clockwise yaw and rolls to the right. This is countered by

mixing roll and yaw inputs of opposite types in the controller. This optimized cyclorotor

has thrust to weight ratio of 3:1 at operational speed of 3000 rpm.

15

(HU, FU, ZHANG, WANG, & FARHAT, 2019) article shows the effects of the aspect

ratio and taper ratio on the cycloidal rotor working at large pitching amplitude using

the Unsteady Reynolds Averaged Navier–Stokes equations (URANS) solver.

According to this paper hover efficiency is measured by figure of merit (FM) which is

the ratio of ideal power to actual power and FM increases slightly with the taper ratio.

However, it was found that improvement of FM is more significant due to airfoil and

chord length than due to larger aspect ratio. The blades with the taper ratio equal to

unity are the most efficient ones. This is due to the FM increases with the blade chord

length when chord/radius ratio (C/R) is smaller than 0.5 and larger the taper ratio closer

it approaches to 0.5. The aerodynamics force coefficients do not vary much with the

aspect ratio. The greater the aspect ratio the more intense and concentrated downwash

in the rotor cage. The efficiency slightly increases with aspect ratio but compared with

the blade airfoil and chord length efficiency does not vary significantly with respect to

aspect ratio. All the simulations were done using ANSYS Fluent and solvers used were:

Incompressible Navier Stokes Equation and Pressure Implicit with Splitting of

Operators. By the observation done by all the simulations and experiments they

concluded that the hover efficiency is more dependent on the unsteady aerodynamic

effects due to the blade pitching motion rather than the blade platform shape and should

pay more attention to the blade airfoil and pitching motion, rather than the blade

platform shape.

This journal (Gagno, Morandini, & Fournier, 2021) focuses mainly on efficiency

optimization. It is known that cycloidal rotor efficiency is highly dependent on rotor

diameter, angular velocity, and other geometric parameters. The important parameter

to consider is weight which directly influences effective energy efficiency. Weight is

interrelated with rotor dimensions and angular velocity, which changes the required

structural strength.

The study reports optimal power loadings for: high chord/radius ratio; short spans; and

solidity σ ≈ 0.4. This article rather finds very low chord/radius and very low solidity.

These discrepancies mostly highlight the different objectives of the two studies and the

impact that the weight and material choice have on payload efficiency. As such, a

simpler analysis could calculate the aircraft mass mt by extrapolation.

16

A minimization technique with one objective function, 7 constraints, and 10 variables

was used to yield an optimal configuration. The resulting configuration was presented

in all its detail and the procedure used can be adapted to different cyclogyro designs.

The whole procedure was carried out using open-source software, mainly the Sage

Math and Dakota toolboxes. The method can also be modified to perform similar

preliminary analyses for other 3D printed aircraft designs that require the optimization

of efficiency. The method easily extends to studying supplementary parameters and

configurations in order to obtain the best compromise between aircraft size, cost, flight

time, flight velocity, efficiency, and payload.

This paper (Cogan & Gagnon, 2022) focuses on creating a model to give a good

overview of the performance of a cyclorotor, trading accuracy for computational speed.

cyclorotor with almost any combination of radius, blade number, profile, rpm, chord

length, and pivot function. The model is tested with six blades, each using a NACA

0012 airfoil. A symmetrical airfoil is chosen because it must provide lift with both a

positive and negative angle of attack.

Experimental thrust and power consumption values for varying cyclorotor

configurations were gathered by the Korea Aerospace Research Institute. To measure

only the aerodynamic effects of the blades, the weight of the scale and structure was

subtracted from the thrust, and the power draw of the cyclorotor without the rotor blades

was subtracted from the gross power draw. Both the maximum pitch angle as well as

the rotational velocity are tested over a wide envelope to obtain a wide variety of results.

The results were obtained from 2D simulation and experimental model. Both were

tested on different configurations varying rotational velocity and pitch. As the critical

angle of attack is reached, the thrust produced dropped initially as flow separation

occurred. However, as the angle of attack increased further, the lift began to increase

again.

Comparing the thrust and power draw of several different CFD configurations, the

thrust is as expected higher than the experimental values. With fewer disturbances and

flow disruptions, the cyclorotor can displace more air in two dimensions than with a

finite wing.

17

### 3 CHAPTER THREE

METHODOLOGY

### 3.1 REVIEW OF LITERATURES

Literature available on the development of cyclorotor, performance of cyclorotor,

control characteristics of cyclorotor and cyclorotor pitching mechanism were reviewed

for the knowledge of design parameter selection, part design realization, pitching

mechanism realization and assembly techniques. Literature also served for simulation

with the solvers dedicated for simulating cyclorotor aerodynamic characteristics. Most

importantly the design parameters for the most optimized cyclorotor were obtained

from the literature.

### 3.2 OBSERVATION

Results and reviews of different experimentalists’ videos on the internet were observed

which offered knowledge on the working of cyclorotor, parts design and assembly

techniques, performance of different cyclorotor models and so on. Online videos for

cyclorotor pitching mechanisms were observed multiple times for better understanding

of the system for implementation on this project.

### 3.3 SOFTWARES EMPLOYED

### 3.3.1 CATIA V5

Catia V5 is a CAD software offering different workbenches for mechanical design and

simulation. We used the software for 3D modeling the parts of our cyclorotor and

simulation of the pitching mechanism. Part design workbench was used to model the

parts of the cyclorotor. Assembly workbench was used for assembling the parts and

components. Similarly, Digital Mockup (DMU) workbench was used to simulate the

pitching mechanism of the cyclorotor. The Generative Shape Design workbench

offered a platform for plotting the airfoil. Drafting workbench provided the platform

for 2D realization of the solid parts.

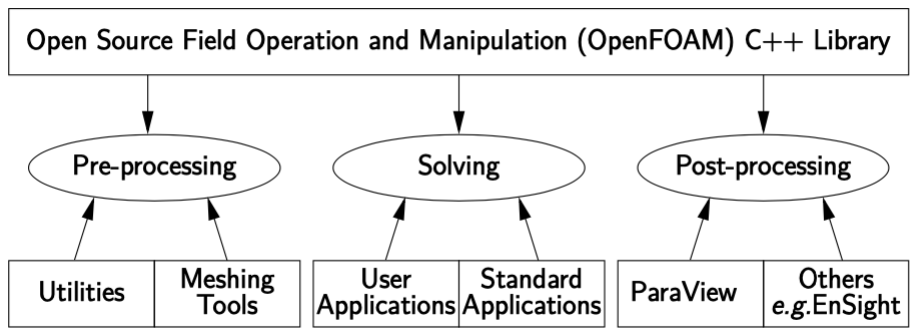
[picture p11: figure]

18

### 3.3.2 XFLR5

XFLR5 is an analysis software for analyzing airfoils and wings. The software offers

different features for modeling and analyzing the aerodynamic parameters of the airfoil.

We utilized the Direct Foil Design workbench for plotting the airfoil and Xfoil Direct

Analysis workbench for analyzing the lift parameters and other aerodynamic

parameters of the airfoil.

### 3.3.3 OpenFOAM

OpenFOAM is a framework for developing application executables that use packaged

functionality contained within a collection of over 100 C++ libraries. OpenFOAM is

shipped with approximately 200 pre-built applications that fall into two categories:

solvers, that are each designed to solve a specific problem in fluid (or continuum)

mechanics; and utilities, that are designed to perform tasks that involve data

manipulation. The solvers in OpenFOAM cover a wide range of problems in fluid

dynamics.

OpenFOAM is supplied with pre- and post-processing environments. The interface to

the pre- and post-processing are themselves OpenFOAM utilities, thereby ensuring

consistent data handling across all environments.

Figure 4 Overview of OpenFOAM structures

OpenFOAM is distributed with a large set of precompiled applications, but users also

have the freedom to create their own or modify existing ones. Applications are split into

two main categories:

19

Solvers are each designed to solve a specific problem in computational continuum

mechanics.

Utilities that perform simple pre-and post-processing tasks, mainly involving data

manipulation and algebraic calculations.

OpenFOAM is divided into a set of precompiled libraries that are dynamically linked

during compilation of the solvers and utilities. Libraries such as those for physical

models are supplied as source code so that users may conveniently add their own

models to the libraries. This chapter gives an overview of solvers, utilities and libraries,

their creation, modification, compilation, and execution.

20

### 3.4 PROJECT FLOW CHART

Figure 5 Project flow chart

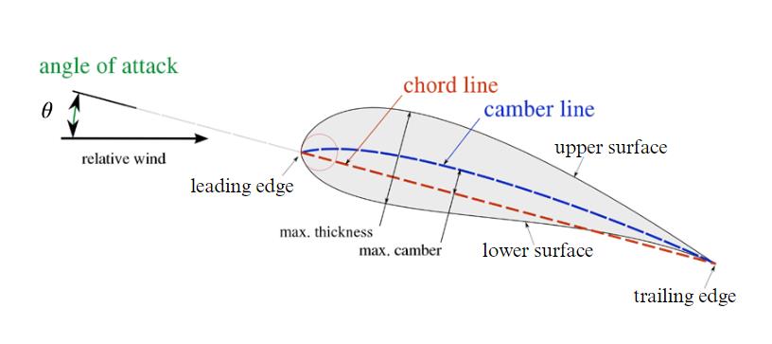
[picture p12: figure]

21

### 4 CHAPTER FOUR

MATHEMATICAL MODELING

### 4.1 AIRFOIL MODELING

An airfoil is a shape of cross-section of wing, turbine and propellers which is designed

such that it can produce desired lift, drag and aerodynamic properties when moved

through a fluid medium such as air or water. Airfoil, although, is a closed shape contour;

its shape can be discretized as shown in the figure below.

Figure 6 Airfoil nomenclature (Source:

https://en.wikipedia.org/wiki/File:Wing_profile_nomenclature.svg)

Airfoil can be classified on the basis of the camber it poses viz; symmetrical and

cambered airfoil. Symmetrical airfoils have upper camber surface and lower camber

surface mirrored about the chord line. The chord line and the camber line coincide in

symmetrical airfoil. Whereas, cambered airfoils tend to have asymmetrical curves on

the upper and lower surfaces. The camber can be positive and negative on the basis of

the curvature orientation of the camber surface.

The coefficient of lift and coefficient of drag for an airfoil is dependent on the angle of

attack (θ) which is the angle between the airfoil chord line and the free stream velocity.

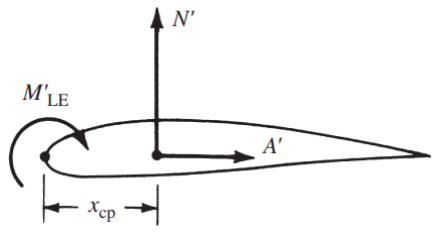
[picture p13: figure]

22

cl = cn cosθ − ca sinθ

cd = cn sinθ + ca cosθ

where cn and ca are the normal force coefficient and axial force coefficient.

Also, the dimensionless aerodynamic parameters can be expressed in terms of

dynamic pressure as follows:

cl =

L

′

q∞c

cd =

D

′

q∞c

cm =

M′

q∞c

2

where cm is coefficient of moment

q∞ is dynamic pressure.

Center of pressure is another important aerodynamic parameter which defines the

stability of the wing body. It is that point on the body about which the aerodynamic

moment is zero.

Mathematically,

xcp = −

MLE

′
L

′

Figure 7 Center of pressure for an airfoil (Source: Fundamental of Aerodynamics,

John.D.Anderson)

When the airfoil displaces fluid existing in its motion path, it produces aerodynamic

forces namely, lift and drag which are functions of different aerodynamics properties.

23

Mathematically,

Lift Force L =

1
2

ρ∞V∞

2SCL

Drag Force D =

1
2

ρ∞V∞

2SCD

### 4.2 CYCLOROTOR

Mathematical modeling of a cyclorotor involves the use of equations that describe the

aerodynamic forces acting on the blades, as well as the motion of the fluid around the

blades. One common approach is to use the Navier-Stokes equations, which describe

the motion of a fluid in terms of its velocity, pressure, and density, and to solve these

equations numerically using computational fluid dynamics (CFD) software.

Mathematical modeling is an important tool for understanding the performance and

behavior of cyclorotor and can help to optimize their design and operation for maximum

efficiency and power output.

Using a new semi-empirical model, the thrust generated, and power required by the

cycloidal rotor can be predicted (Leger, Pascoa, & Xisto, 2015). This is the important

part of the design as it helps to analyze different parameters like:

1. Size of blade chord relative to the cyclorotor's radius
2. To describe eccentricity point
3. Positing of the pivot point and distance between connection point of control rod

and pivot point

4. Position of blades according to eccentricity phase angle
5. Distance between the blades

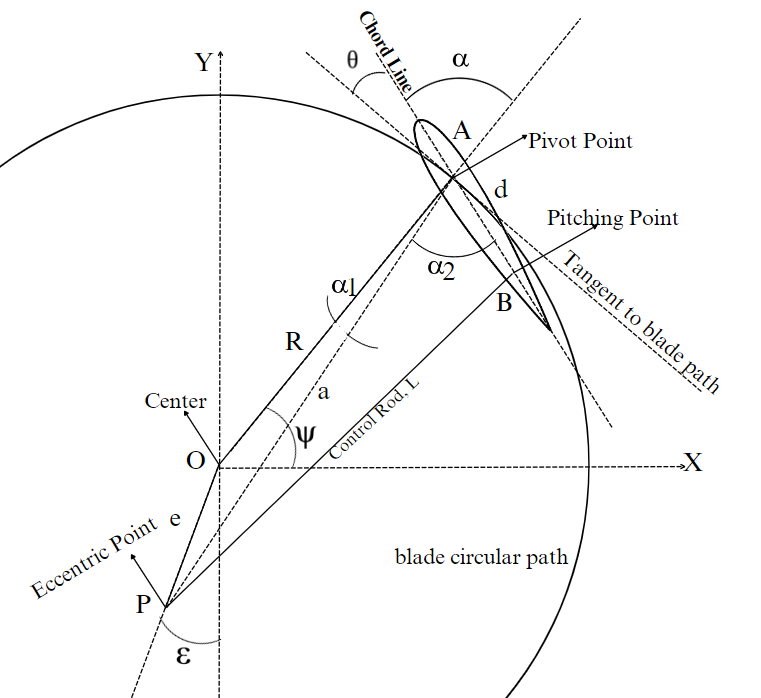
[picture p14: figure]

24

### 4.2.1 KINEMATIC MODEL

Figure 8 Blade control mechanism schematic

Here

Ψ = | azimuth angle
θ = | Angle of attack
e = | eccentricity distance
ε = | eccentricity phase angle (phase angle)
d = | distance between pivot point and pitching point
l = | distance between eccentric point and pitching point
R = | distance between center and pivot point
a = | distance between eccentric point and pivot point

25

From figure 8

θ =

Π
2

− α

α = α1 + α2

In ΔOAP

sin(α1)
e

=

sin(

Π
2

+ ε + ψ)
a

In ΔPAB

cos(α2) =

a

2 + d

2 − l

2
2ad

Therefore

θ =

Π
2

− sin⁻¹
[

e
a

cos(ψ + ε)] − cos⁻¹
[

a

2 + d

2 − l

2
2ad ]

In general azimuth angle for different blades can be obtained by

ψi(0) = ψ1(0) +

(i − 1)2π
N

Where ψ1(0) is one blade initial location and N is the number of blades.

The leading edge and trailing edge coordinates are given by (Leger, Pascoa, & Xisto,

2015):

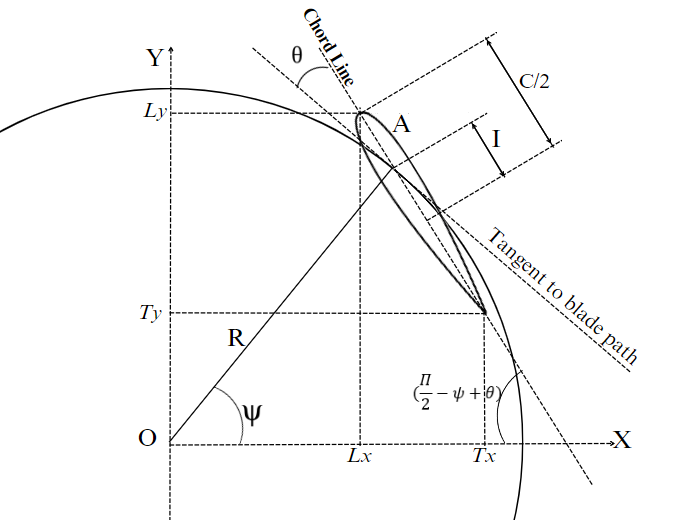
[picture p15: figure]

26

Figure 9 Leading and trailing edge coordinates

From figure 9

Lx = Rcos(ψ) − (

c
2

+ I)cos(

Π
2

− ψ + θ)

Ly = Rsin(ψ) + (

c
2

+ I)cos(

Π
2

− ψ + θ)

Tx = Rcos(ψ) + (

c
2

− I)cos(

Π
2

− ψ + θ)

Ty = Rsin(ψ) − (

c
2

− I)cos(

Π
2

− ψ + θ)

### 4.2.2 AERODYNAMIC ANALYSIS

Figure 10 represents the dynamic forces applied to the cyclorotor blade in hovering

state. Here L is the lift, D is the drag, VR is the resultant velocity associated with the

induced downwash angle Φ.

27

Figure 10 Horizontal and vertical resultant force components of blade in hovering state

(Leger, Pascoa, & Xisto, 2015)

The resultant forces in horizontal and vertical direction are given by:

Fx = Lcos(ψ − φ) + Dsin(ψ − φ)

Fy = Lsin(ψ − φ) − Dcos(ψ − φ)

The induced downwash angle is given by:

φ = tan⁻¹

VN

VTG

The tangential component of resultant velocity is VRcosφ and the normal component is

VRsinφ.

The tangential velocity due to the rotor rotational movement is given by.

VT = ΩR

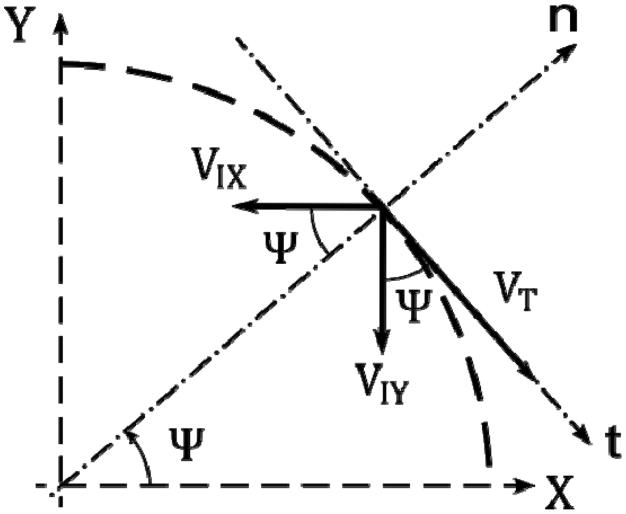
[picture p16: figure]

28

Figure 11 Analysis of induced velocities (Leger, Pascoa, & Xisto, 2015)

Figure 11 shows the induced down washed velocities depicted where VIX is the induced

velocity in horizontal direction and VIY is the induced velocity in vertical direction.

The resultant velocity in tangential and normal direction are given by.

VTG = VT − VIXsin(ψ) + VIYcos(ψ)

VN = −VIXcos(ψ) − VIYsin(ψ)

Now the induced velocities as the function of Φ can be expressed as

VIX = VTsin(ψ) − VRsin(ψ + φ)

VIY = VRcos(ψ + φ) − VTcos(ψ)

The 3-D lift curve of the cyclorotor airfoil is given by (McNabb, 2001)

CLα3D =

2ΠAR
2 + √(
AR

2 4Π²

CIα

2 + 4)

The two-dimensional unsteady lift is given by (Leger, Pascoa, & Xisto, 2015)

29

L
S

= ρb

2
(VRπω − πbIacc) + CLα3DρVRbF[VR(θ + φ) + b(

1
2

− I)ω]

+

CLα3DρVRbG
Ω

[VRω + b(

1
2

− I)acc]

### 4.3 TRANSMISSION GEAR AND BELT

### 4.3.1 GT2 TIMING PULLEY

GT2 timing pulley is a toothed type of pulley used in power transmission systems in

highly accurate positioning equipment. The teeth on the pulley provide proper

engagement and prevent slippage during operations. “GT2” designation of this pulley

refers to the type of the tooth profile used and stands for “Gates Tooth 2” in the honor

of Gates Corporation who developed it.

The tooth profile features a trapezoidal shape with rounded root and a circular top

providing higher torque transmission capacity, lower backlash, and reduced noise

compared to other tooth profiles. GT2 timing pulley is designed specifically to work

with GT2 timing belts.

The design of GT2 tooth profile involves different parameters and they are

interdependent as well. Equations representing their relations can be shown as below:

1. Pitch Diameter (PD) - The diameter of the pulley where the belt makes contact. PD = (N ∗ TP) / π

where N is the number of teeth in the pulley.

2. Outside Diameter (OD) - The maximum diameter of the pulley.
OD = PD + 2 ∗ TH
3. Root Diameter (RD) - The minimum diameter of the pulley where the belt enters

the tooth groove.
RD = PD − 2.5 ∗ TP
4. Tooth Height (TH) - The distance from the bottom of the tooth groove to the

pitch diameter.
TH = BT ∗ 2.17
5. Belt Thickness (BT) - The thickness of the belt. BT = 0.64 ∗ TP

30

6. Tooth Pitch (TP) - The distance from the center of one tooth to the center of the

next tooth.

TP = 2 ∗ T / (N + 2)

where T is the belt pitch

7. Tooth Profile Angle (TPA) - The angle between the tooth face and a line

perpendicular to the pulley axis.

TPA = atan((TH − BT) / (π ∗ PD / N − TP))

Since this tooth profile is designated as GT2 there are constraints to some parameters

of the tooth such as.

- Tooth Height
- Tooth Pitch (which is 2mm since it is GT2)

### 4.3.2 GT2 TIMING BELT

GT2 timing belt refers to tooth type belt which has GT2 type tooth profile, specifically

designed to work with GT2 timing pulley. The design parameters involved are same as

that of the GT2 timing pulley, however the belt width and the belt length are the main

constraints that are required to be carefully chosen. Guiding parameters for the selection

of the belt are pitch of the belt (2mm for GT2 specifically), center-center distance

between two pulleys, number of teeth on driver and driven pulley and torque to be

transferred.

The belt length is a crucial parameter in belt selection and is dependent on the above-

mentioned parameters. The belt length of a GT2 timing belt can be calculated using the

following relation:

L = 2C +

((N2 + N1

) ∗ P)
2

+

((N2 − N1

)

2
∗ P

2
)
4π

2C

Where L is the belt length, C is the center-center distance between the two pulleys, N1

and N2 are the number of teeth on the driving and driven pulleys respectively and P is

the pitch of the belt.

31

### 4.4 LOAD CELL

A load cell is a weight sensor which converts the force applied on it into an electrical

signal measured in volts. The measured volt is then calibrated to the proper scale

according to the sensitivity of the load cell and hence then used. The output voltage of

a load cell can be calculated using the equation,

Vout = (

F
A

) ∗ (

E
2

) ∗ (L2 − L1)

Where F is force applied, A is the area of the load cell, E is the modulus of elasticity

and L2 and L1 are the lengths of the load cell under load and without load, respectively.

Sensitivity is the ratio of change in output to the change in load applied to the load cell.

This is the measure of the ability of the load cell to detect small changes in load applied.

The sensitivity can be calculated using the expression,

S = (Voutmax − Voutmin) / Fmax

Where Voutmax and Voutmin are the maximum and minimum output voltages respectively

and Fmax is the maximum rated capacity of the load cell.

32

### 5 CHAPTER FIVE

MATERIALS AND COMPONENTS SELECTION

### 5.1 MATERIALS FOR FABRICATION

### 5.1.1 PLA FILAMENT

PLA (Polylactic Acid) filament is a type of plastic that is commonly used in 3D

printing. It is made from renewable resources, such as corn starch or sugarcane, and it

is biodegradable, making it a more environmentally friendly option than some other

types of 3D printing filament. PLA filament is known for its ease of use, as it is typically

easier to print with than other materials, such as ABS (Acrylonitrile Butadiene Styrene).

It has a lower melting temperature than ABS and is less prone to warping or shrinking

as it cools, which makes it suitable for a wide range of 3D printing applications.

PLA filament is available in a range of colors and can be used to create a wide range of

3D printed objects, from prototypes and models to finished products. It is often used

for educational or hobbyist projects, as well as for more professional applications. The

mechanical properties of PLA filament depend on several factors, including the specific

grade of PLA that is used, the processing conditions, and the environment in which the

printed object is used. In general, PLA filament has the following mechanical

properties:

1. Tensile strength: The tensile strength of PLA filament is typically in the range

of 50-80 MPa (Megapascals). This is the maximum stress that the material can

withstand while being stretched or pulled before it breaks.

2. Tensile modulus: The tensile modulus of PLA filament is typically in the range

of 1200-3000 MPa. This is a measure of the stiffness of the material, and it

indicates how much the material will deform under a given load.

3. Impact strength: The impact strength of PLA filament is typically in the range

of 20-40 kJ/m². This is a measure of the material's ability to absorb energy when

it is struck or impacted.

33

4. Hardness: The hardness of PLA filament is typically in the range of 80-90 Shore
D. This is a measure of the material's resistance to indentation and scratching.

Figure 12 PLA filament spool

### 5.1.2 ALUMINUM TUBE

Aluminum is a lightweight and strong metal that is used in a wide range of applications,

including the manufacture of tubes. The mechanical properties of aluminum tubes

depend on several factors, including the specific alloy of aluminum that is used, the

manufacturing process, and the condition of the material. The aluminum tubes available

in the market are manufactured from different grades of aluminum (1000 – 7000 series).

Here are some general mechanical properties of aluminum tubes:

1. Tensile strength: The tensile strength of aluminum tubes is typically in the range

of 180-620 MPa (Megapascals). This is the maximum stress that the material

can withstand while being stretched or pulled before it breaks.

2. Yield strength: The yield strength of aluminum tubes is typically in the range of

60-350 MPa. This is the stress at which the material begins to deform

permanently.

3. Modulus of elasticity: The modulus of elasticity of aluminum tubes is typically

in the range of 69-73 GPa (Gigapascals). This is a measure of the stiffness of

the material, and it indicates how much the material will deform under a given

load.

4. Density: The density of aluminum tubes is typically around 2.7 g/cm³. This is a

measure of the mass of the material per unit volume.

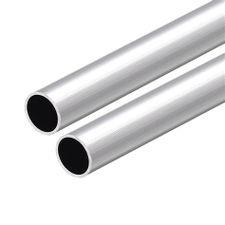
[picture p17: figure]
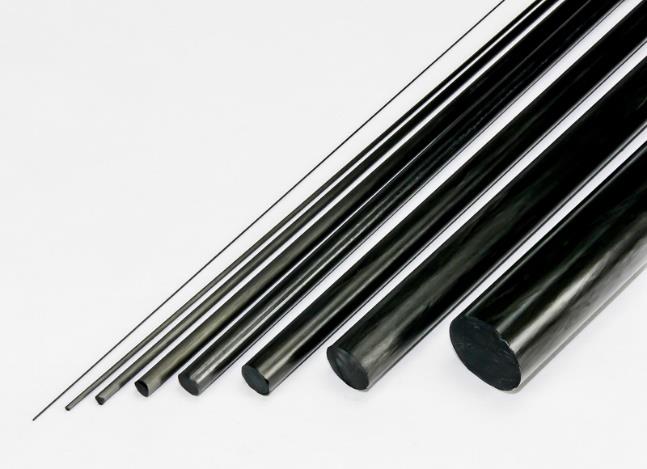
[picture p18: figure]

34

5. Thermal conductivity: The thermal conductivity of aluminum tubes is typically

around 205 W/m K. This is a measure of the material's ability to conduct heat.

Figure 13 Aluminum tube

### 5.1.3 CARBON FIBER ROD

Carbon fiber is a polymer that is a very strong lightweight material. They have several

advantages including high stiffness, high tensile strength, low weight, high chemical

resistance, high temperature tolerance and low thermal expansion. Carbon fiber is five-

times stronger than steel and twice as stiff. Mechanical parameters of the carbon rod

can be referred to from appendix A table 6.

Figure 14 Carbon fiber rod

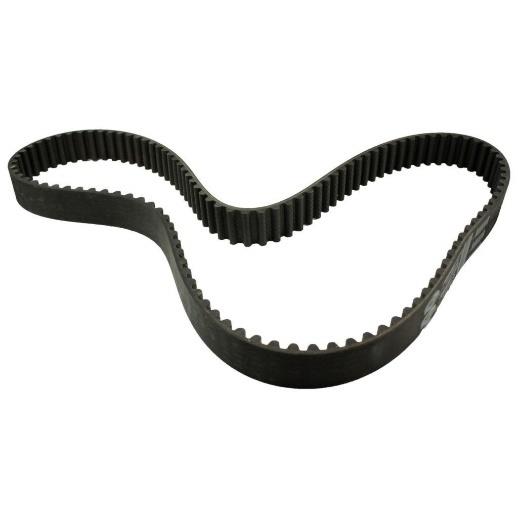
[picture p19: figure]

35

### 5.2 COMPONENTS

### 5.2.1 GT2 TIMING BELT

The GT2 Belt is a timing belt built with Neoprene rubber with fiberglass core. It comes

with an open loop or closed loop. The open loop belt is long and can be used by cutting

it to our desired length however the closed loop has fixed length and number of teeth.

The ‘GT2’ in its name refers to the specific tooth profile of the gear manufactured by

Gates Corporation. The GT2 belt benefits in precision positioning, quieter operation,

slip proof engagement, and higher power transmission efficiency.

Figure 15 GT2 timing belt

5.2.2 1400 KV BRUSHLESS DC (BLDC) MOTOR

A 1400KV brushless DC (BLDC) motor is a type of electrical machine that converts

electrical energy into mechanical energy. It is called a brushless motor because it does

not have brushes, which are used to transfer electrical current in traditional DC motors.

Instead, brushless motors use electronic commutation, in which the phase of the

electrical current is electronically controlled to produce rotational motion.

Brushless DC motors are known for their high efficiency, low maintenance, and good

speed control. They are often used in applications where these characteristics are

important, such as electric vehicles, robotics, and industrial automation. The 1400KV

rating of the motor indicates that it can produce a high amount of torque for its size and

weight, which can be useful in applications where a compact and powerful motor is

36

required. KV is a measure of the voltage that is required to produce one thousand RPM

(revolutions per minute) of the motor's rotor.

Figure 16 1400 KV Brushless DC motor

### 5.2.3 ELECTRONIC SPEED CONTROLLER (ESC)

An Electronic Speed Controller (ESC) is an electronic circuit that is used to control the

speed of an electric motor, such as the motor in a brushless DC motor. The ESC receives

a signal from a controller, such as a radio transmitter or a microcontroller, and uses this

signal to adjust the amount of power that is delivered to the motor. By controlling the

power to the motor, the ESC can control the speed of the motor.

ESCs are commonly used in radio-controlled models, such as drones, planes, and cars,

to control the speed of the motors that drive the model. They are also used in other

applications where the speed of an electric motor needs to be controlled, such as

robotics, electric vehicles, and industrial automation.

ESCs are usually designed to work with a specific type of motor, such as a brushless

DC motor or a brushed DC motor. It is important to choose an ESC that is compatible

with the motor that you are using, to ensure that the motor is supplied with the correct

amount of power and that it operates safely. Since the power requirement for our model

is very low being the test model small enough, we have selected 30 Amp ESC for this

project which will serve our desired control of the motor.

37

Figure 17 30A Electronic Speed Controller

### 5.2.4 LITHIUM POLYMER BATTERY

A lithium polymer battery (also known as a Li-poly or LiPo battery) is a type of

rechargeable battery that uses lithium-ion technology. It is called a "polymer" battery

because the electrolyte that carries the lithium ions between the anode and cathode is

suspended in a polymer matrix, rather than being a liquid as in traditional lithium-ion

batteries. LiPo batteries are known for their high energy density, which means that they

can store a lot of energy in a small space. This makes them a popular choice for portable

electronic devices, such as smartphones, laptops, and tablets, as well as for radio-

controlled models, such as drones and remote-controlled cars.

One of the main advantages of LiPo batteries is that they can be charged and discharged

very quickly, making them ideal for applications that require rapid changes in power

output. However, they can be more sensitive to abuse, such as overcharging or puncture,

than other types of batteries, so it is important to use and handle them with care.

Figure 18 LiPo Battery 2200 mAh 3S

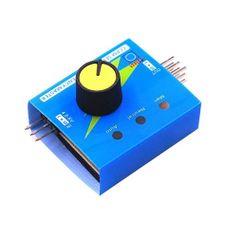
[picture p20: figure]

38

### 5.2.5 SERVO TESTER

A servo tester is a device that is used to test and calibrate servo motors. Servo motors

are a type of electrical motor that is commonly used in radio-controlled models, such

as drones and remote-controlled cars, as well as in robotics and industrial automation

applications.

A servo tester typically consists of a power supply, a controller, and a display. It allows

the user to send a signal to the servo motor and observe its response, such as its position

or speed. This can be useful for diagnosing problems with the servo motor, adjusting

its performance, or verifying that it is functioning correctly.

Servo tester can also be used to test a BLDC motor by connecting the servo tester with

the ESC and powering the ESC with the battery. Here in this project, the servo tester

serves both the function of actuating BL DC motor and a servo motor.

Figure 19 Servo tester

### 5.2.6 STEEL BOLTS AND NUTS

Steel bolts and nuts are fasteners that are used to hold two or more parts together. They

consist of a bolt, which is a threaded rod with a head at one end, and a nut, which is a

threaded cylinder that is tightened onto the bolt. Steel is a common material for bolts

and nuts because it is strong, durable, and resistant to corrosion. There are many

different grades of steel that are used for bolts and nuts, each of which has its own

specific characteristics and properties. The most common grades of steel for bolts and

nuts are grade 2, grade 5, and grade 8.

39

Grade 2 steel is a low-strength steel that is often used for light-duty applications. It is

easy to work with and has good resistance to corrosion, but it is not as strong as higher-

grade steels.

Grade 5 steel is a medium-strength steel that is often used for medium-duty

applications. It is stronger and more durable than grade 2 steel, but it is still relatively

easy to work with.

Grade 8 steel is a high-strength steel that is often used for heavy-duty applications. It is

the strongest and most durable of the common steel grades, but it is also the most

difficult to work with.

Bolts and nuts are available in a range of sizes and thread pitches to suit different

applications. It is important to choose the correct size and grade of bolt and nut for the

specific application to ensure that the fastener is strong enough to hold the parts together

and that it is compatible with the other components in the system.

Highlighting the size of the test model and light application, grade 2 steel 3mm bolts

and nuts have been used in this project along with compatible washers. Since the model

is made of polymer and has much less strength compared to that of steel, we can assure

the bolts and nuts will not fail during its operation.

### 5.2.7 STEEL MACHINE SCREWS

Steel machine screws are fasteners that are specifically designed for use with machine

parts. They are made from a harder and more durable material, such as steel or stainless

steel, and they have a more precise thread pitch than general screws. Steel machine

screws are typically used with a tapped hole, which is a hole that has been threaded to

match the thread pitch of the screw. This allows the screw to be tightened securely into

the hole and ensures that it holds the parts together with a high level of precision.

The machine screw used in this project came along with the brushless motor which we

procured. The screw is used to mount the motor to the motor mount and hence fixes the

motor rigidly to the substrate.

40

Figure 20 Steel machine screw

### 5.2.8 LOAD CELL

A load cell, also known as a weight sensor or strain gauge, is a device that is designed

to measure a specific force in one direction. It consists of a carefully designed metal

structure with small elements called strain gauges mounted in precise locations on the

structure. When a load is applied, the structure deforms and the strain gauges measure

the deformation, which is then converted into an electrical signal that can be amplified

and measured. Load cells are made of aluminum alloys and are sensitive to forces only

along the vertical direction as prescribed by the manufacturer. They require a load cell

amplifier such as the HX711 load cell amplifier or the 1046 PhidgetBridge for electrical

signal output.

Figure 21 Load cell

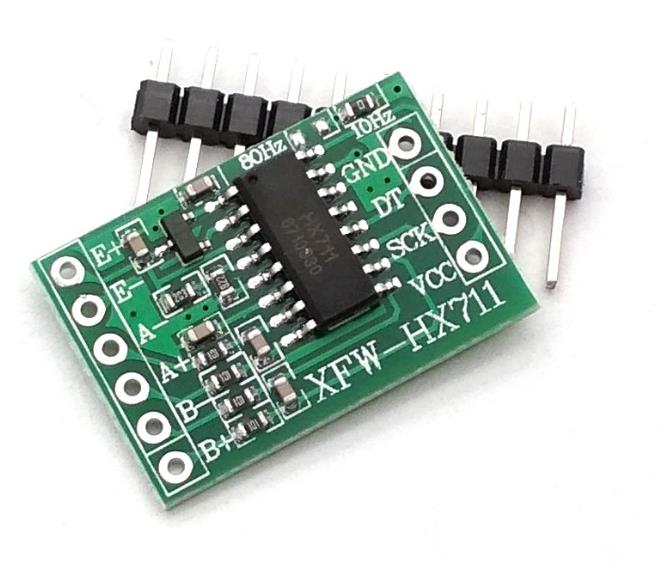
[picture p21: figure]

41

### 5.2.9 HX711 MODULE

The HX711 module is an amplifier that provides an interface to communicate with the

load cell. This module is named HX711 since it is engraved with the HX711 chip which

has 24 high precision A/D converters. This includes an on-chip low-noise amplifier

(LNA) that can amplify the small signals from the load cell or strain gauge to make

them more easily measurable. The HX711 can operate from a single power supply and

has two differential input channels that can be used to connect to the load cell or strain

gauge. The module also includes a programmable gain amplifier (PGA) that allows the

user to adjust the gain of the amplifier to match the specific needs of the application.

The module can interface with a microcontroller using its library which is available

open source. The HX711 library offers the interface for calibration as well as the read

test facility which provides real time data acquisition.

Figure 22 HX711 Amplifier

### 5.2.10 ARDUINO UNO

The Arduino Uno is a microcontroller board based on the ATmega328P. It has 14

digital input/output pins, 6 analog inputs, a 16 MHz quartz crystal, a USB connection,

a power jack, an ICSP header, and a reset button. It is widely used in various DIY

projects, robotics, and electronic devices. It can be programmed using the Arduino

software, which is based on C/C++ programming languages. The board can be powered

either through the USB connection or an external power supply. It has a built-in voltage

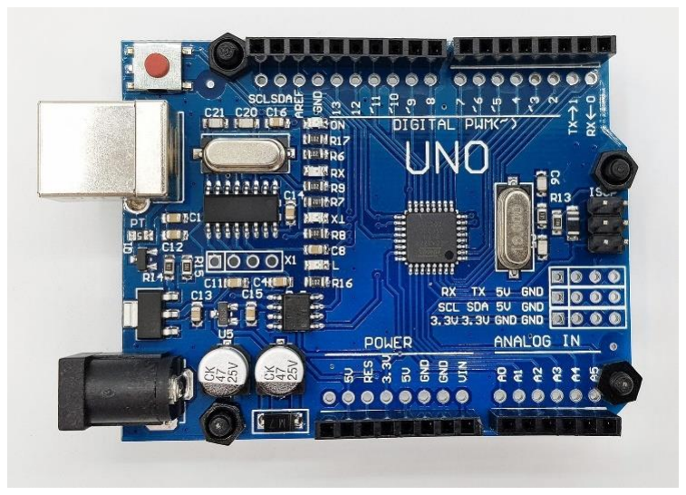
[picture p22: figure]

42

regulator that can regulate the input voltage between 7V to 12V. The board also has a

wide range of shields, which can be used to extend its functionality.

Figure 23 Arduino Uno

43

### 6 CHAPTER SIX

DESIGN, SIMULATION AND ANALYSIS

### 6.1 AIRFOIL DESIGN AND ANALYSIS

Airfoil design is very crucial on a project like this since the primary functioning part of

the system to meet the objective is the airfoil blade. Airfoil is responsible for producing

the desired lift when it is subjected to moving air. Although there are different

parameters responsible for generation of lift, characteristics of lift generation are also

important according to the system that the airfoil blade has been employed on. Our

system has a feature such that one airfoil can contribute twice to lift generation in one

revolution of the rotor allowing both the surfaces of the airfoil blade to contribute

according to its position in the plane of rotation. Due to this unique feature of the

cyclorotor the airfoil to be used in this system requires both the surfaces to produce

equal and adequate lift during operation which is possible only with the symmetric

airfoil. Hence symmetric airfoil has been used in this project.

Although the symmetric profile of the airfoil has been selected, specific type and design

parameters of airfoil are difficult to state. For this reason, we have chosen NACA0015

airfoil with 2-inch chord since it has been found to be an optimal airfoil for the

cyclorotor from previous experiments (Benedict, Jarugumilli, & Chopra, Effect of

Rotor Geometry and Blade Kinematics on Cycloidal Rotor Hover Performance, 2013).

Analysis of NACA0015 airfoil using XFLR5 software with Reynolds number 39,941 (calculation shown in later section) and the angle of attack varying from -10o

to 60o

with increment of 0.3o
gives the following polar curves. The curve shows that the value

of coefficient of lift increases with increase in angle of attack. The value of coefficient decreases sharply after 9o

. As the angle of attack increases further than 9o
the coefficient

of lift starts to increase again. This is called post-stall lift. Since for this experiment the maximum angle of attack that the cyclorotor blade will encounter is 40o
hence the
coefficient of lift corresponding to the 40o
angle of attack obtained from the curve is

1.21.

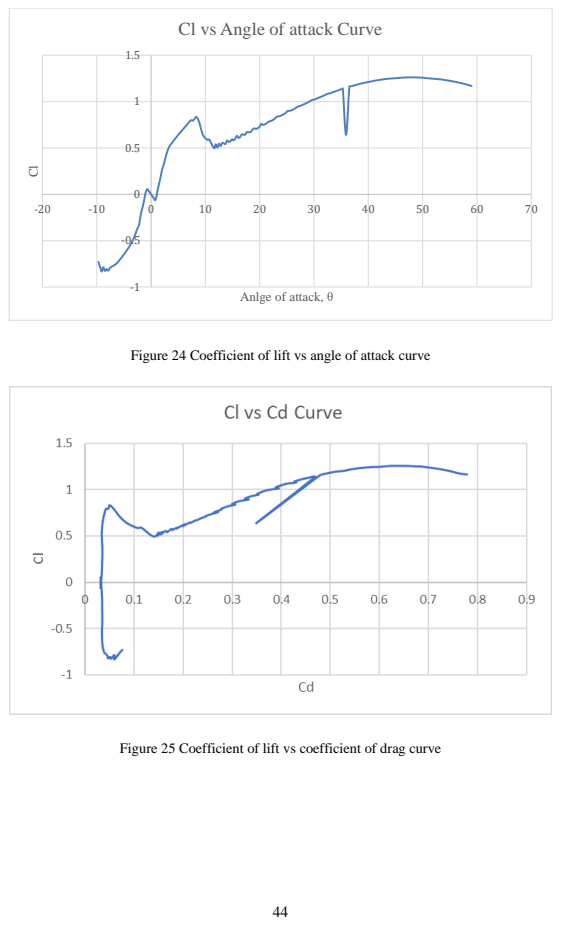
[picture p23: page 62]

Cl vs Angle of attack Curve

Anlge of attack, θ

Figure 24 Coefficient of lift vs angle of attack curve

Figure 25 Coefficient of lift vs coefficient of drag curve

45

Numerical calculation for obtaining the maximum lift produced

Chord length | = 50.8 mm
Density of air | = 1.225 kg/m⁻³
Area | = 50.8 × 10 −3 × 171 × 10

−3= 8.686× 10

−3 m²

RPM | = 1400
⍵ | = 146.607 rad /s
velocity (v) | = 11.17 m/s

Kinematic viscosity (ν) = 1.42*10⁻⁵

Reynolds number (Re
) =

v.l
ν

=

11.17×0.0508
1.42×10⁻⁵

= 39,941

Maximum lift force | = 2 * lift produced by each blade = ⍴ ∗ v
| 2 ∗ A ∗ Cl
| = 1.225 × 11.17 2 × 8.686 × 10 −3
∗ 1.21
| = 1.6063 N
| = 163.74 g

### 6.2 ROTOR DESIGN

Rotor design involves consideration of several factors to ensure proper function ability

and efficient operation of the cyclorotor. A rotor is an assembly of mainly two parts:

airfoil blade and rotor wheels. The main factor that is to be considered on the airfoil

blade after aerodynamics is the strength of the airfoil blade so that it can bear the

46

bending stress and shear stress generated due to lift produced during the operation.

Similarly, for the rotor wheel, tensile stress is a major consideration since the point of

joints transfer tension produced by the virtue of lift generation by blade holder element.

Efficient cyclorotor is the key requirement of this project as its object is to study the

thrust vector curve generated due to the variation in eccentric phase angle.

### 6.2.1 ROTOR WHEEL

Much research had been done previously where the objective was to develop an

efficient and optimized cyclorotor. Referring to those research and experiments, some

design parameters for our experiment have been chosen based on optimized and

efficient cyclorotor.

The radius of the rotor is chosen to be 3 inches which is claimed to be a proven optimal

design parameter (Benedict, Chopra, & Gupta, Design, Development and Open-Loop

Flight-Testig of a Twin-Rotot Cyclocopter, 2013). The 3-inch rotor radius gives the

chord/radius ratio of 0.67 which is in the range of 0.5 and 0.8 and shows viability

according to the statement presented in the previous literature. The maximum amplitude of pitching is chosen 40o
as per the same literature since these constraints define the

cyclorotor to be optimal.

Considering the carbon spar element to be undeform-able and rigid (to be discussed in

subsequent sections) we design the rotor wheel impact site portions. The force applied

to the site is by the carbon rod fitted inside the hole of the rotor wheel and is tensile or

compressive according to its position in the plane. The lift generated is the amount of

load applied to the sites hence, limiting our maximum lift attainable to 200 grams we

calculate the tensile stress on the rotor wheel section.

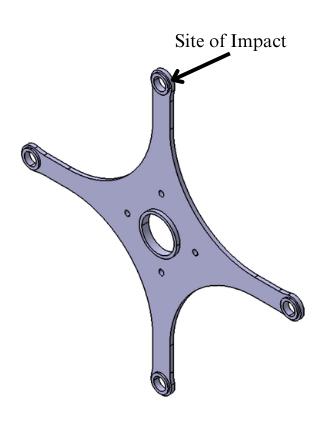
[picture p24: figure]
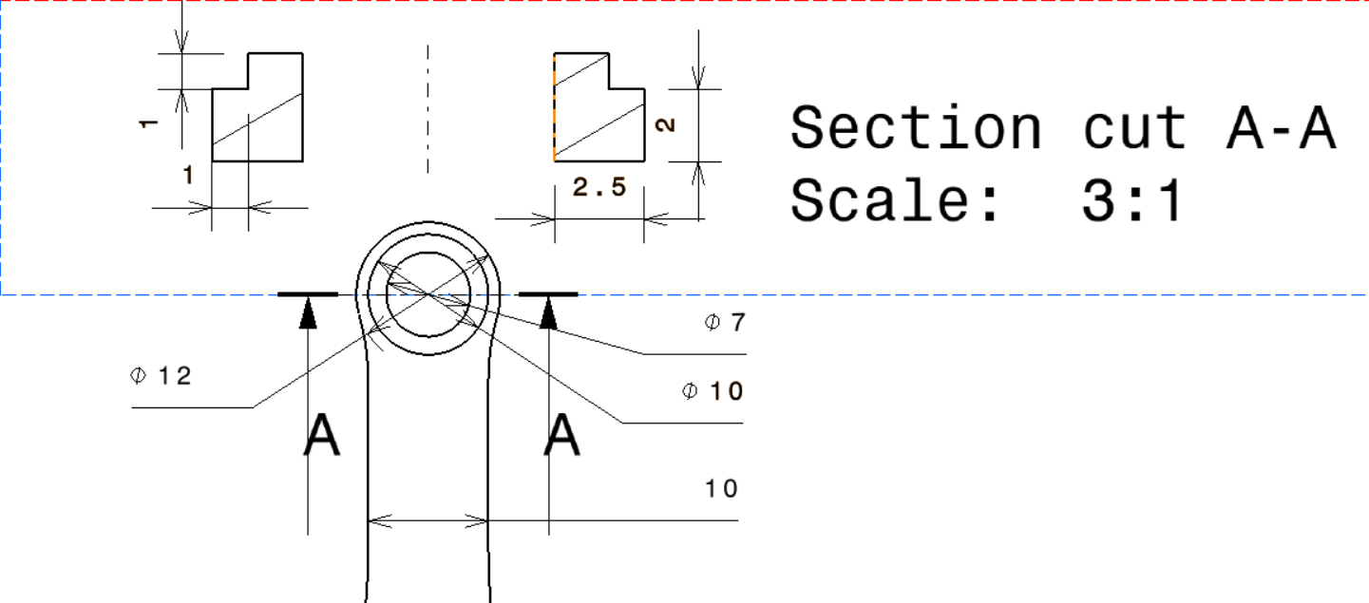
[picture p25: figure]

47

Figure 26 Rotor wheel tensile stress vulnerable site

Since two blades are responsible for lift generation at once, the contribution of each

blade is equal. Hence the lift generated by each blade is 100 grams. Again, the blade is

attached to the two rotor wheels on each end and lift force acts from the center of the

blade, each rotor joint point will experience 50 grams of lift force. Hence taking the

force of 50 grams as the load applied, we find the tensile stress on the section of the

rotor.

Figure 27 Section of the vulnerable impact site

Tensile Stress | σ =

F
A

48

Where F = 50 grams = 0.4905 N

and A = 2 ∗ ((2.5 ∗ 2) + (1.5 ∗ 1)) = 13 mm²

Hence, tensile stress

σ = 37,730.77 Pa

The strength of the material used to manufacture the part is in the range of 50 – 80 MPa

hence the part will not fail in tension during operation.

### 6.2.2 AIRFOIL BLADE

Aerodynamics regarding the airfoil has been discussed in the preceding section, thus

this section will be oriented on the mechanical parameters of the airfoil blade i.e., the

strength of the airfoil blade. Before proceeding with the mechanical strength of the

blade, the blade dimension is paramount. From literature review it is found that the

optimal configuration for a cyclorotor is the blade span equal to the rotor diameter

(Kirsten, 1928). Again, the latest experiment from (Benedict, Chopra, & Gupta, Design,

Development and Open-Loop Flight-Testig of a Twin-Rotot Cyclocopter, 2013) shows

that the most optimal configuration of cyclorotor has a blade span of 6.25 inch. Hence

referring to those results and statement the blade is set to 171 mm (~6.7 inch). The extra

blade span resulted from the mount that is used to hold the blade hence giving an

effective blade span as 6.25 in.

The blade is subjected to bending stress and shear stress due to the lift which is acted

uniformly throughout the blade. The carbon rod is used as the reinforcing element and

contributes for assembling the airfoil blade to the rotor wheel as well. From Figure 23

we can see that the blade loading is of simply supported beam type with uniformly

distributed lift force acting throughout the length of the blade. Hence the bending stress

and shear stress can be computed using the uniformly distributed lift force of 0.5848

gram/mm in each blade. The reinforcement is provided by two carbon fiber rods; hence

the bending stress will be experienced by both the rod along with the surface of the

blade.

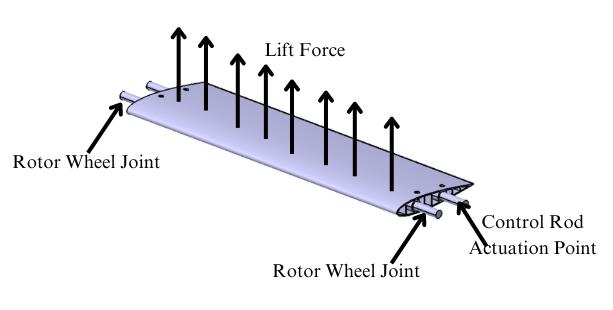
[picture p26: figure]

49

Figure 28 Blade force diagram

Shear stress can be calculated using the following relation.

τ =

4V
3A

Where A = 12.5664 mm²

V = 50 gram (from appendix A figure 61)

Hence the maximum shear stress that exists on the carbon rod is 52,043.6664 Pa.

Bending stress on the blade element is calculated as,

σm =

Mc
I

Where c = 2mm

I = 12.5664 mm⁴

M = 2137.5 gm mm (from appendix A figure 62)

Hence the maximum bending stress persists at the center of the spar length and the

magnitude of the stress is 3.3373 MPa.

From the appendices table 3 we can compare that the stresses generated are much lower

than their limits hence the carbon fiber rod of 4 mm is viable for our use in the project.

50

If the optimal design is considered the diameter of the carbon rod can be much lesser

as 1 mm, however, for ease of fabrication this dimension is restrained for this project.

The best location of the airfoil pitching axis is at 25 % of the chord from the leading

edge of the airfoil (Shrestha, Yeo, Benedict, & Chopra, 2017). Considering all the

factors that have been well studied and experimented with previously our design

parameters were obtained as shown in the table below.

Table 1 Design parameters for the cyclorotor used in this project.

S.No | Parameter | Value
1 | Rotor Diameter | 152.4 mm
2 | Total Blade Span | 171 mm
3 | Chord Length | 50.8 mm
4 | Pitching axis location | 25% of chord from leading edge
5 | Actuation point in airfoil | 17.5 mm from Pitching axis
6 | Total length of control rod | 76.2 mm
7 | Carbon Rod Spar | 4 mm (diameter)

51

### 6.3 TRANSMISSION DESIGN

### 6.3.1 GEAR DESIGN

A GT2 timing pulley has been used in this project for transferring the power from motor

to the cyclorotor. The selection of the gear pulley involves torque requirement and

speed requirement. In this project the torque offered by the motor is adequate hence

torque multiplication factor shall not be of paramount interest rather the speed is crucial

since the RPM range is limited on the lower range for cyclorotor. Because our model

has been experimented with 4800 RPM in recent experiments, we allocate the

maximum RPM for our cyclorotor as 5000 RPM. The driver gear is chosen of 20 teeth

since 5 mm bore diameter is the main constraint and with this requirement of bore size

other lower size of the driver pulley is not possible and another bigger option is not

chosen due to dimensional limitations. The driven gear has 60 teeth. This set of gear

gives a torque multiplication factor 3, being the speed reduction factor 3. The

calculation has been shown below:

Constraints

Motor specification: | 1400 KV
Maximum obtainable RPM: | 15540 RPM (with 3S battery)
Required range of RPM: | 0 - 5000 RPM
Minimum size of GT2 timing pulley available: | 20 Teeth / 5mm Bore (appendices

figure)

Calculation for gear ratio

Gear Ratio | =

Max RPM available on tℎe motor sℎaft Max RPM required on tℎe cyclorotor sℎaft

=

15400
5000

= 3.108

Rounding off the value and taking the integer only, the gear ratio is 3.

52

Calculation for number of teeth required on driven GT2 timing pulley required.

Number of teeth required | = Number of Teetℎ in Driver Gear ∗ Gear Ratio

= 20 * 3

= 60 Teeth

### 6.3.2 BELT DESIGN

Belt design involves belt width and belt length determination along with the tooth

profile. For the case of GT2 timing pulley, GT2 timing belt is specifically manufactured

by the manufacturer. Hence the design parameters are the belt width and the belt length

for this project. The pitch of the belt to be used is 2 mm since it is a GT2 timing belt,

and the center-to-center distance is 58 mm set according to dimensional feasibility in

the model. With the data provided the belt length is obtained to be 198.7951 mm and

the belt length in catalog near to this value is 200 mm. Hence a 200 mm GT2 timing

belt has been used.

For the width of the belt, table 5 from appendix A is referred which shows that 1 mm

width has 86 N breaking strength which is more than required but since 1 mm width

belt is not available and the lowest size available is 6 mm, it is chosen for the cyclorotor

driver system.

### 6.4 SIMULATION OF CYCLOROTOR

The CFD model is tridimensional and uses the finite volume method to solve the

PIMPLE algorithm, which consists of a merger of the PISO and SIMPLE algorithms.

OpenFOAM is used for the simulation of the model.

### 6.4.1 SOLVERS

In this project pimpleFoam is used. pimpleFoam uses the PIMPLE algorithm. The

PIMPLE algorithm combines the PISO (Pressure Implicit with splitting of operations)

and SIMPLE (Semi-Implicit Method for Pressure Linked Equations) algorithm. This

algorithm is an iterative procedure for coupling equations of momentum conservation

and momentum conservation. The PIMPLE algorithm is mainly used for transient

53

problems. Within steps, in time this algorithm solves a pressure equation to enforce

mass conservation, with an explicit correction to velocity to satisfy momentum

conservation. The principle of this algorithm is as follows.

Within a single time-step, a steady-state solution is searched while an under-relaxation

strategy is applied. After the solution is found, we go to the next time-step. For this, we

need the so-called outer correction loops, to ensure that all explicit parts of the equations

are converged. After a user-defined tolerance criterion is reached within the steady-

state calculation the outer correction loop is left, and we move on in time. This is done

until the simulation end time is reached (Greenshields C. J., 2018).

Outer correctors: The number of Outer correctors of the PIMPLE algorithm defines

how many outer iterations to perform, that is, how many times the system of equations

are performed before it is forced to move onto the next time step, regardless of whether

that time step has converged or not. If the step convergence is reached before the

number of iterations is reached, then it will stop and move on to the next time step. The

(Greenshields C. , 2018)criteria for time step convergence are defined as the absolute

tolerance of the solver (SimScale, 2020).

Inner correctors: The number of inner correctors is the number of times the pressure

is corrected within an iteration. Typically, this should be set low. Many correctors rarely

improve results and should conform to this recommendation.

The PIMPLE algorithm below is cited and explained as proposed by Holzmann

(Holzmann, Mathematics, numerics, derivations and OpenFOAM®, 2019).The steps

from 1 to 4 represent the first loop, while the correcting second loop begins on step 5,

each one coupling pressure and momentum once.

Construct momentum matrix:

Ut | + ∇. (UU) + ∇. R | = | −∇. p

Construct the pressure matrix using the momentum matrix.

| ∇

2p = f(U, ∇p)

Calculate pressure.

54

pnew

Correct the velocities with the new corrected field.

pnew → Ucorrected

Reconstruct the momentum matrix with new velocities.

U
δt + ∇. (UU) + ∇.R = −∇p

Construct the pressure matrix using the momentum matrix with the new velocities.

∇

2p = f(U, ∇p)

Calculate pressure.

pnew

Correct the velocities with the new pressure field.

pnew → Ucorrected

### 6.4.2 TURBULENCE MODELING

Turbulent phenomena occur temporally, as well as spatially, fine scales, extreme

computing resources would be required to investigate them using basic CFD methods.

This is the case for 'Direct Numerical Simulations' (DNS), which are rarely practical,

because they demand extremely fine grid spacings and time steps. To treat turbulent

phenomena in a more efficient way, multiple, mostly empirical turbulence models have

been designed by CFD engineers. The choice is the commonly used URANS-method

(unsteady Reynolds averaged Navier-Stokes), which models turbulent variables like

velocity u and pressure p using a statistically averaged (e.g., u) and a variable

component (u′):

u = u + u′

55

Applying the above equation to the Navier-Stokes-equations leads to the expression

u′v′. These terms are difficult to close, which is why semi-empirical models are

commonly used, adding up to 2 transport-equations. In the current work, k-ω-SST-

Model is the method of choice.

### 6.4.3 THE SST K-ω TURBULENCE MODEL

The SST k-omega turbulence model is a two-equation eddy-viscosity model that is used

for many aerodynamic applications. The k-ω model is the model of choice in the

sublayer of the boundary layer. Unlike any other two-equation model, the k-/omega

model does not involve damping functions and allows Dirichlet boundary conditions to

be specified. Because of its simplicity the k-ω model is superior to other models in case

of numerical stability. It is also as accurate as other models in predicting flow profile.

### 6.4.4 ARBITRARY MESH INTERFACE (AMI)

To simulate rotating motion, Arbitrary Mesh Interface (AMI) is used in OpenFOAM.

The inner zone rotates relative to the outer zone. The AMI interpolates inner and outer

mesh to achieve a coupling of two meshes that are rotating relative to each other. In

OpenFOAM cyclic AMI boundary conditions can be used to couple these zones. In our

project a total of 5 moving mesh use sliding interfaces of interpolation. They are solved

by the Arbitrary Mesh Interface (AMI) algorithm. Each rotor blade is inserted into a

double AMI. The outer AMIs rotate, and the inner ones strongly oscillate. The inner

cell zone includes the blade surfaces and are referred to as AMI-cylinders. To avoid

sharp corners, which are generally detrimental to mesh quality, the AMI-cylinders have

a hemispherical base area. (Donners, 2022)

### 6.4.5 MESHING

The background mesh between the cylinders and the far field is created using

OpenFOAM's automatic meshing tool snappyHexMesh. blockMesh is used to create

cartesian structured grid. The snappyHexMesh automatically refines specified areas,

snap to surfaces and is also capable of adding boundary layers. The resulting grid is

hexahedral unstructured.

56

The | snappyHexMesh | utility generates 3-dimensional meshes containing hexahedra

(hex) and split-hexahedra (split-hex) automatically from triangulated surface

geometries in Stereolithography (STL) format. It then refines the volume mesh near

and on surfaces in portions of surfaces that are close to other surfaces and inside user-

defined regions. Refinement is applied as a user-specified number of subdivisions to

the original structured mesh. Cells are refined either inside or within a specified

distance of a given region or when intersecting a given surface. Once the mesh is

refined, the cell faces are moved to smoothly adhere to the boundaries, which can be

wall boundaries or simple reference geometries. This last option allows us to create the

sliding interfaces of the blade oscillating zones and the rotor spinning zones. The size

of the (Holzmann, Mathematics, numerics, derivations and OpenFOAM®, 2019) mesh

and the time it takes to generate are controlled by quality and iteration options

(Holzmann, Mathematics, numerics, derivations and OpenFOAM®, 2019).

It is notable that the mesh only includes the airfoils as aerodynamic surfaces, but not

the axle nor any rods. This is to keep the interfaces simple, as rods would require

multiple surfaces that are in direct contact and nevertheless moving relative to each

other. Furthermore, the aerodynamic influence of these surfaces is expected to be

limited to moderate power losses, which is why this simplification is deemed

permissible. (Donners, 2022)

Figure 29 Refined mesh sphere

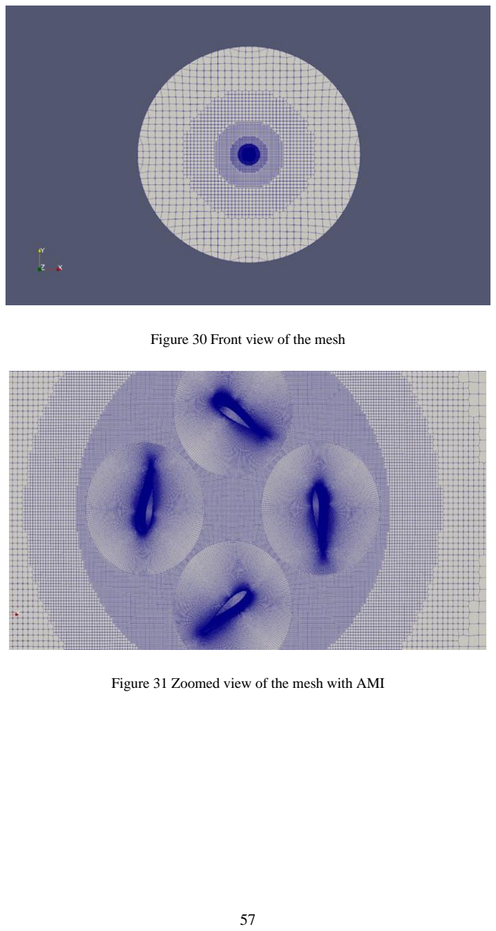
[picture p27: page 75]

57

Figure 30 Front view of the mesh

Figure 31 Zoomed view of the mesh with AMI

58

Table 2 Statistic inspection of mesh

Pitching angle Mesh at | Data Type | No. of Cells | No. of Points | Memory (MB) | Geometry Size (MB)
45 | Multiblock Dataset | 6154053 | 3356160 | 1112.948 | 110.352
90 | Multi-block Dataset | 6107608 | 3236995 | 1090.64 | 112.308
135 | Multi-block Dataset | 5959071 | 3250438 | 1078.025 | 105.105
180 | Multi-block Dataset | 5281492 | 2817824 | 947.537 | 90.588
225 | Multi-block Dataset | 5656766 | 2987188 | 1010.477 | 97.701
270 | Multi-block Dataset | 6108598 | 3238636 | 1090.978 | 112.274
315 | Multi-block Dataset | 5944126 | 3240709 | 1075.081 | 104.953
345 | Multi-block Dataset | 5293087 | 2821693 | 949.31 | 90.776

### 6.4.6 BOUNDARY CONDITIONS:

The boundary conditions are set to specify patch’s types and flow properties at the

edges of the domains. In the following, the hemispherical far-field will be referred to

as far-field, while the airfoil surfaces will be called blades. The patches defining the

interpolation interface are called AMI. Table shows the specified boundary conditions

for U, p, k, ω and νt.

59

| Farfield | Blades | Symmetry | AMI
U | Type pressureInletOutletVelocity value uniform (0 0 0) | Type movingWallVelocity value uniform (0 0 0) | Type symmetry | Type cyclicAMI value uniform (0 0 0)
P | Type totalPressure value uniform 0 | Type zeroGradient | Type symmetry | Type cyclicAMI value uniform 0
k | Type inletOutlet inletValue uniform 0.002099 value uniform 0.002099 | Type kLowReWallFunction value uniform 0.002099 | Type symmetry | Type cyclicAMI value uniform 0.002099
ω | Type inletOutlet inletValue uniform 13.201 value uniform 13.201 | Type omegaWallFunction value uniform 13.2019 | Type symmetry | Type cyclicAMI value uniform 13.201
νt | Type calculated value uniform 0 | Type nutLowReWallFunction value uniform 0 | Type symmetry | Type cyclicAMI value uniform 0

60

### 6.4.7 MOTION OF BLADES

The rotor motion is obtained by rotating the background mesh and AMI-cylinder

around the rotor center. The pitch function is applied to each AMI cylinder to achieve

oscillation around its center and thus blades pitching Motion. The position of the

pitching rod is changed in the function to recreate the change in pitching of the

cyclorotor. (Donners, 2022)

### 6.4.8 SIMULATION

A total of 8 simulations were done varying the pitching angle of the cyclorotor.

pimpleFoam was used as a solver. The mesh was refined using refined surfaces. The

mesh gets more refined as it gets closer to the solver. Time step of 3.6e-4 was taken.

The cyclorotor is rotating at 1400 RPM. The value of kinematic pressure (p) is obtained

which is used to calculate the forces in X and Y direction.

Table 3 Simulation parameters

S.No | Parameters | Values
1 | Flow velocity | (0,0,0)
2 | Kinematic pressure(m² /s² ) | 0
3 | RPM | 1400
4 | Center of rotation | (0,0,0)
5 | Axis of rotation | (0,0,1)
6 | Center of rotation (Pitching motion) | (0.1,0,0)
7 | Incident velocity of air for each blade | 11.17 m/s

61

### 6.4.9 POST PROCESSING:

In simulation, post-processing refers to the process of analyzing and interpreting the

results of a simulation after it has been completed. This can involve visualizing the

results in graphs or plots, calculating statistical measures such as mean and standard

deviation, or comparing the results to experimental data or other simulations. The goal

of post-processing is to extract meaningful insights and information from the simulation

results that can be used to understand the system being simulated and make informed

decisions about its design or operation. Here we obtain the values of lift. The steps are:

1. Extracting the surface from the mesh.
2. Generating surface normal.
3. The lift is obtained by multiplying the surface normal with the pressure.

Let
ny = normals along y

nx = normals along x

Then,
Force along x − direction(Fx) = nx ∗ p

Force along y − direction(Fy) = ny ∗ p

Tℎrust = √Fx
2 + Fy

2

Tℎrust angle = tan⁻¹ (

Fy
Fx

)

The thrust angle is measured with the X-axis as a reference line.

62

Table 4 Simulation results

The graph shown is plotted from the values obtained from simulation done at 8 different

pitching angles. The graph obtained by plotting the forces in X and Y direction vs the

pitching angle is sinusoidal in nature. We can also see that these two graphs are opposite

in nature, i.e., at maximum force in X direction there is min Force at Y direction and

vice versa. The resultant of these two forces is found to be almost constant in all 8

simulations at different pitching angles.

Pitching Angle | Force along X axis | Force along Y axis | Resultant thrust | Thrust angle
0 | 0 | 112 | 122 | 90
45 | -79.4667 | 88.066667 | 118.61993 | 132.062
90 | -126.8 | 0 | 126.8 | 180
135 | -82.53333 | -85.6 | 118.9079943 | 226.045
180 | 0 | -119.46667 | 119.466667 | 270
225 | 84.93333 | -88.3 | 122.5175951 | 313.887
270 | 123.83333 | 0 | 123.833333 | 360
315 | 89.4 | 88.466667 | 125.77457 | 404.699
360 | 0 | 122.03333 | 122.0333333 | 450

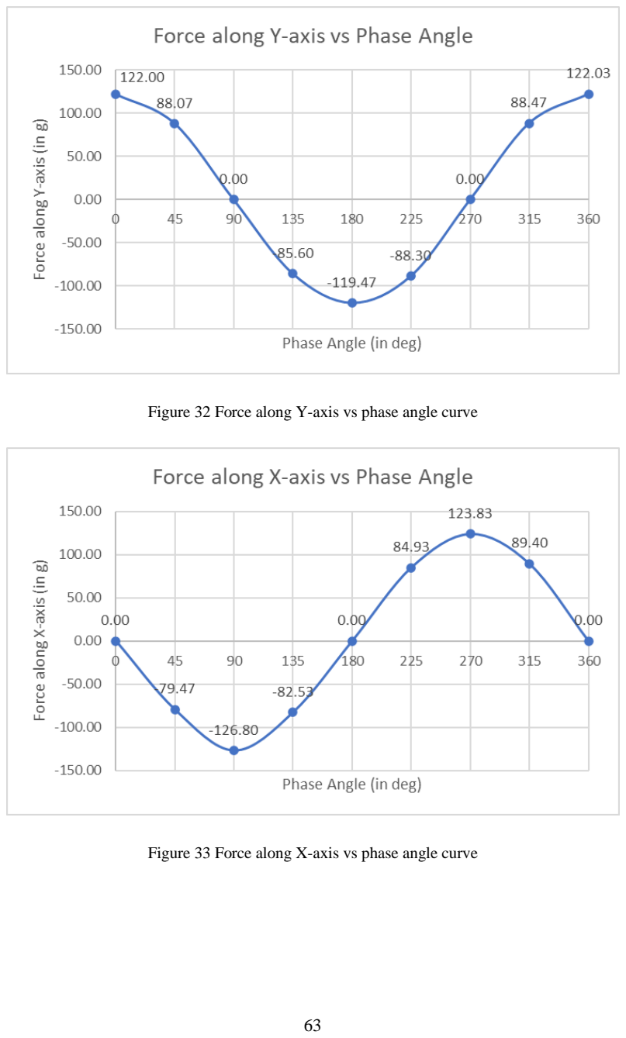
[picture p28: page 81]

63

Figure 32 Force along Y-axis vs phase angle curve

Figure 33 Force along X-axis vs phase angle curve


64

Figure 34 Thrust direction vs phase angle curve.

Figure 35 Thrust vs phase angle curve.

65

### 7 CHAPTER SEVEN

MANUFACTURING AND ASSEMBLY

### 7.1 FABRICATION

### 7.1.1 CYCLOROTOR

Cyclorotor is a product and hence is an assembly of many parts which are brought

together in an organized way such that the product functions as desired by the designer.

It is important to have individual parts designed and manufactured to the accuracy so

that they fit right on their counterparts or other parts where they are meant to be fitted.

The parts of the cyclorotor are modeled using CATIA software and manufactured using

a 3D printing manufacturing process. Below section describes each part of the

cyclorotor in detail.

### 7.1.1.1 MAIN ROTOR WHEEL


Main rotor wheel is the rotating part of the

cyclorotor where the blades are attached. The

rotor wheel has GT2 gear pulley attached to it

concentrically and hence is responsible for

receiving the power from the motor and

rotating the airfoils to meet its prime objective.

The rotor is seated on the main shaft which

runs along the full length and beyond the rotor.

The rotor is assembled such that it can rotate

about the axis of the main shaft. The main shaft

fixes the whole rotor to the body of the aircraft.
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

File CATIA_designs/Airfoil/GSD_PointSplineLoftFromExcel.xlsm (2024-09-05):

StartLoft
StartCurve
0 | 38.1 | 0.0600075
0 | 37.82570286 | 0.10790301
0 | 37.33378995 | 0.19274028
0 | 36.71005104 | 0.29841825
0 | 35.98723689 | 0.41830752
0 | 35.18534238 | 0.54819423
0 | 34.31855595 | 0.68503038
0 | 33.3978123 | 0.8264652
0 | 32.43196968 | 0.97062798
0 | 31.42847664 | 1.11597186
0 | 30.39374922 | 1.2611862
0 | 29.33343003 | 1.40513943
0 | 28.25257113 | 1.54682571
0 | 27.15572547 | 1.68533064
0 | 26.047065 | 1.81979697
0 | 24.93042639 | 1.94940936
0 | 23.80938342 | 2.07339057
0 | 22.68725841 | 2.19096336
0 | 21.56717937 | 2.30136954
0 | 20.45209905 | 2.40386616
0 | 19.34481018 | 2.49771408
0 | 18.24796071 | 2.5821894
0 | 17.16409191 | 2.65660251
0 | 16.09561551 | 2.72027523
0 | 15.04485942 | 2.77257891
0 | 14.01405249 | 2.81293062
0 | 13.00534356 | 2.84080077
0 | 12.02079765 | 2.85573597
0 | 11.06242644 | 2.85734379
0 | 10.13216541 | 2.84532324
0 | 9.23188908 | 2.81946096
0 | 8.36342625 | 2.77962741
0 | 7.52855238 | 2.72580735
0 | 6.72898578 | 2.65805793
0 | 5.96641428 | 2.57654679
0 | 5.24247237 | 2.4815292
0 | 4.55876025 | 2.37333663
0 | 3.91684383 | 2.25238437
0 | 3.31824711 | 2.11915248
0 | 2.76446742 | 1.97416674
0 | 2.25696399 | 1.81800246
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

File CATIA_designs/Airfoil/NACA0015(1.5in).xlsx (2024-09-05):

X(mm) | Y(mm)
38.1 | 0.0600075
37.82570286 | 0.10790301
37.33378995 | 0.19274028
36.71005104 | 0.29841825
35.98723689 | 0.41830752
35.18534238 | 0.54819423
34.31855595 | 0.68503038
33.3978123 | 0.8264652
32.43196968 | 0.97062798
31.42847664 | 1.11597186
30.39374922 | 1.2611862
29.33343003 | 1.40513943
28.25257113 | 1.54682571
27.15572547 | 1.68533064
26.047065 | 1.81979697
24.93042639 | 1.94940936
23.80938342 | 2.07339057
22.68725841 | 2.19096336
21.56717937 | 2.30136954
20.45209905 | 2.40386616
19.34481018 | 2.49771408
18.24796071 | 2.5821894
17.16409191 | 2.65660251
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

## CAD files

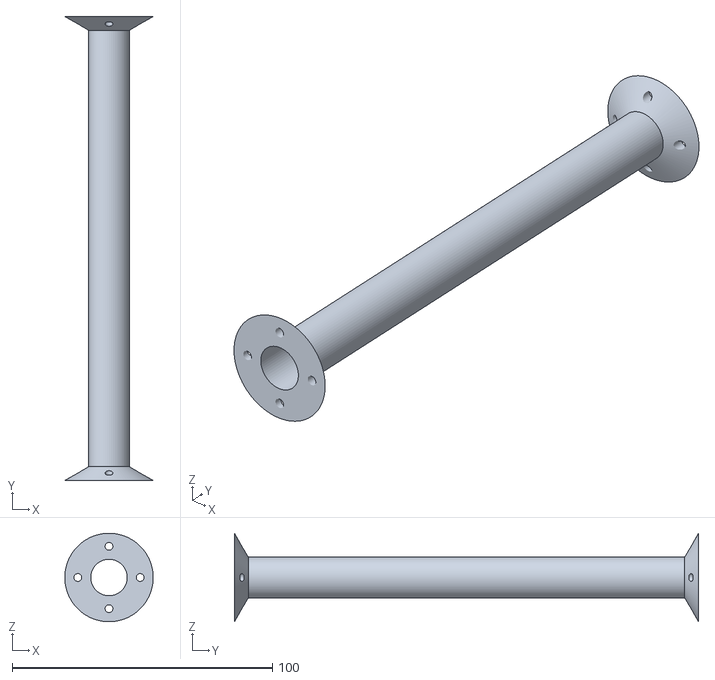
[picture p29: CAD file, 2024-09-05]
CATIA_designs/Cyclorotor_Parts/Main Rotor Separator Shaft.stl
34.0 x 178.4 x 34.0

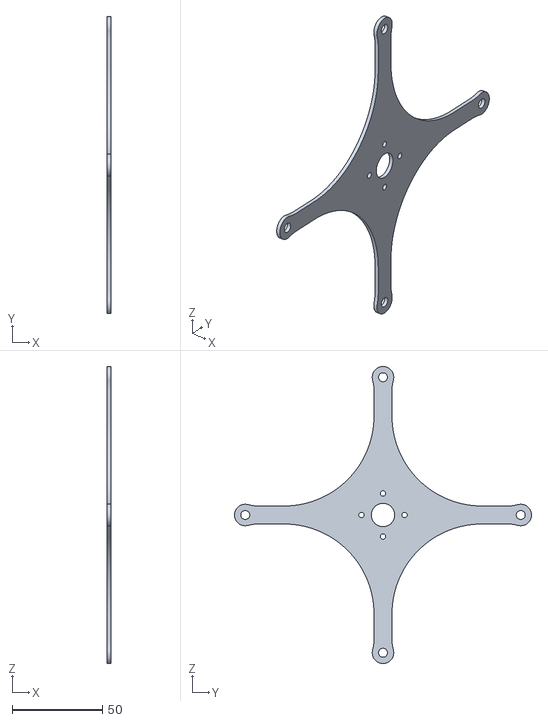
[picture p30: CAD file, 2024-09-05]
CATIA_designs/Cyclorotor_Parts/Main Rib Wheel.stl
2.00 x 165.0 x 165.0

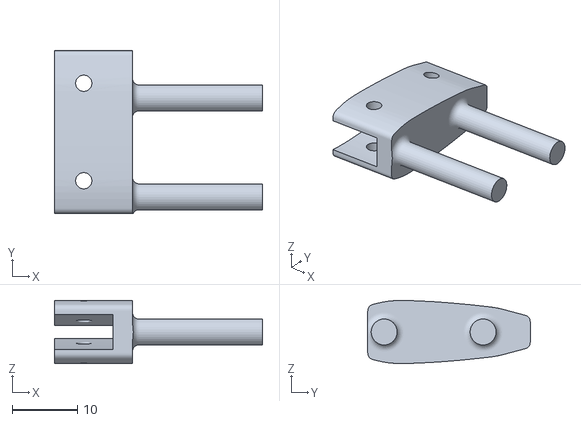
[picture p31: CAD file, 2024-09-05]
CATIA_designs/Airfoil/Airfoil holder 1.5in.stl
32.0 x 25.0 x 9.71

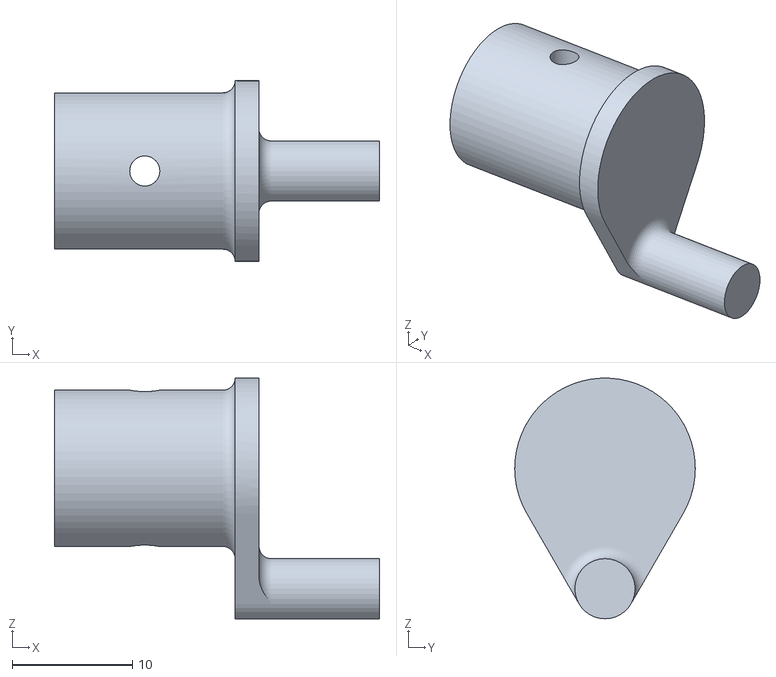
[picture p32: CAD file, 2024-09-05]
CATIA_designs/Cyclorotor_Parts/Servoshaft Coupler (Outboard).stl
27.0 x 15.0 x 20.0

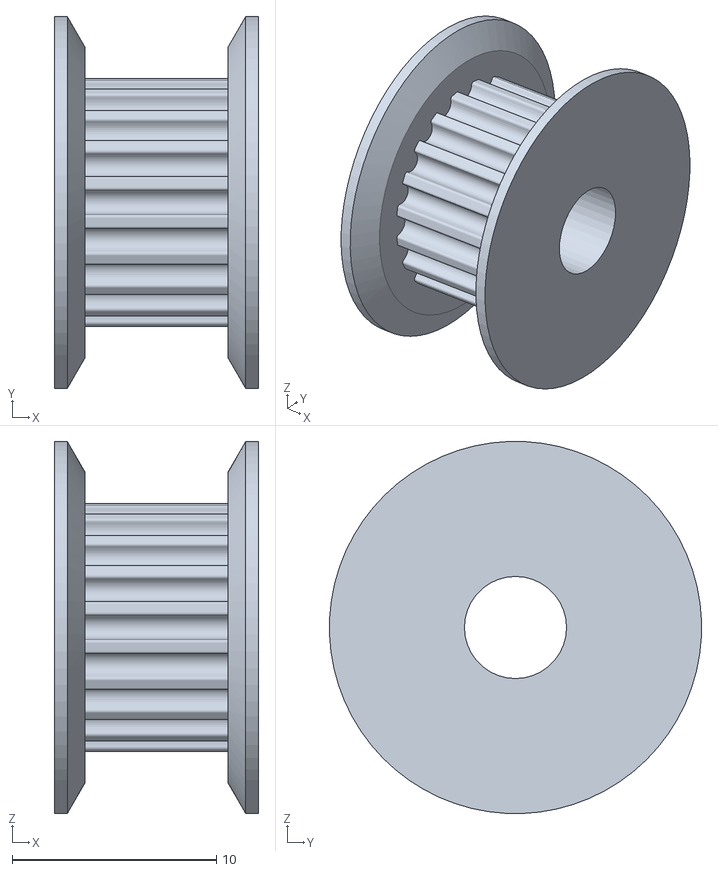
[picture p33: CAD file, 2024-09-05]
CATIA_designs/Gear_Pulleys/Gear pulley 20T.stl
10.0 x 18.2 x 18.2

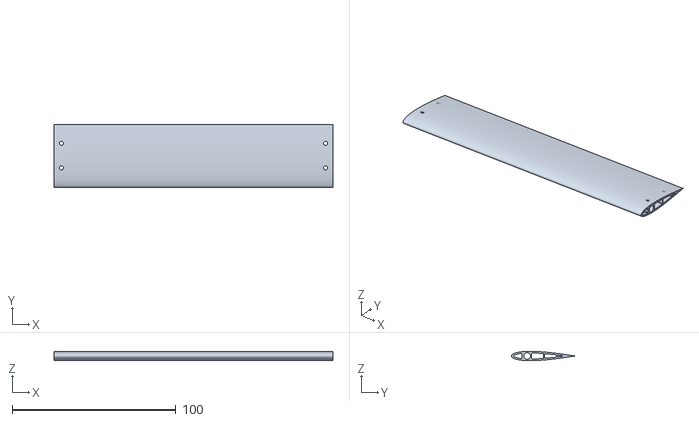
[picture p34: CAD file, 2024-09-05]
CATIA_designs/Airfoil/NACA0015 (1.5in).stl
170.4 x 38.4 x 5.72

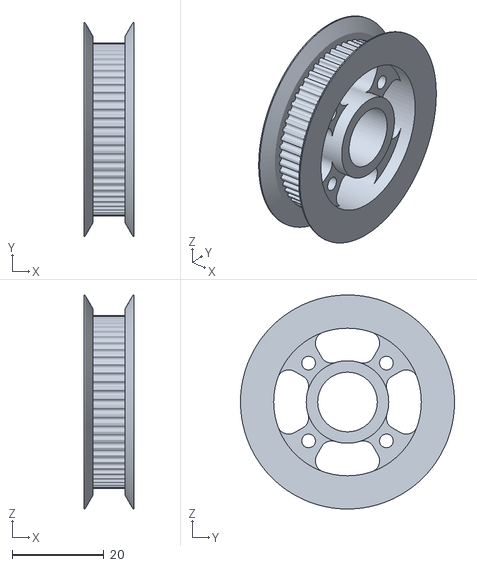
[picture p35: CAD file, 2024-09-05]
CATIA_designs/Gear_Pulleys/Gear pulley 60T.stl
11.0 x 46.7 x 46.7

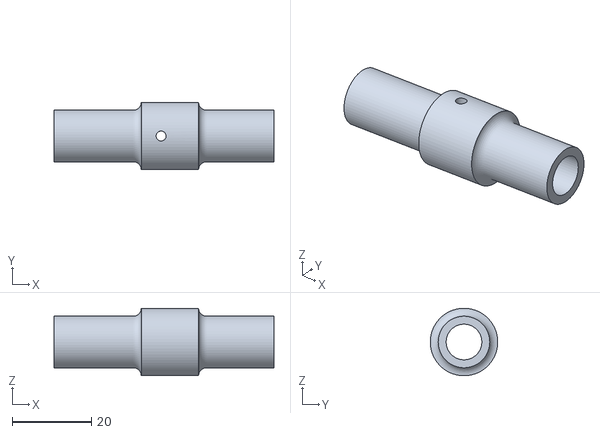
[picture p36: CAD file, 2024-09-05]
CATIA_designs/Cyclorotor_Parts/Servoshaft Coupler (Inboard).stl
55.5 x 17.0 x 17.0

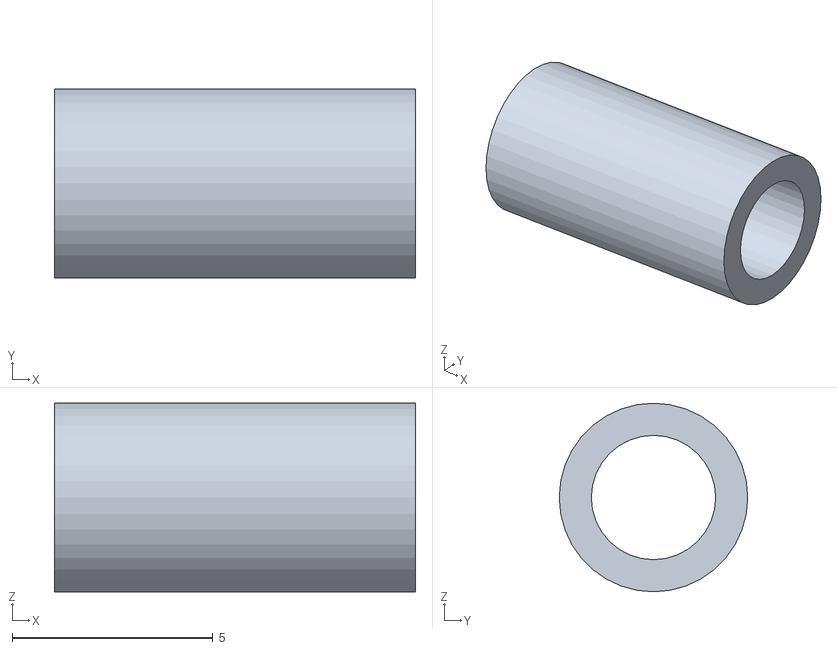
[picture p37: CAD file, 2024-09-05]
CATIA_designs/Cyclorotor_Parts/Separator.stl
9.00 x 4.70 x 4.70

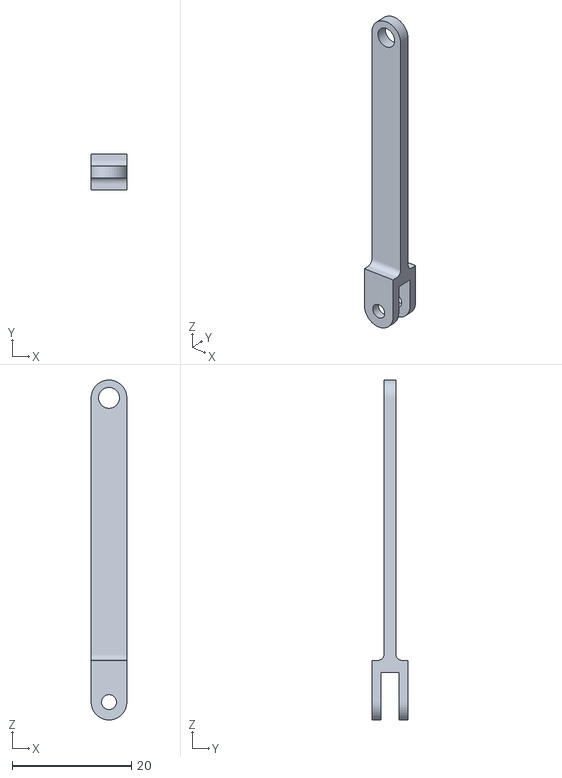
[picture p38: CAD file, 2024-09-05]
CATIA_designs/Cyclorotor_Parts/Controlrods.stl
6.00 x 6.00 x 57.0

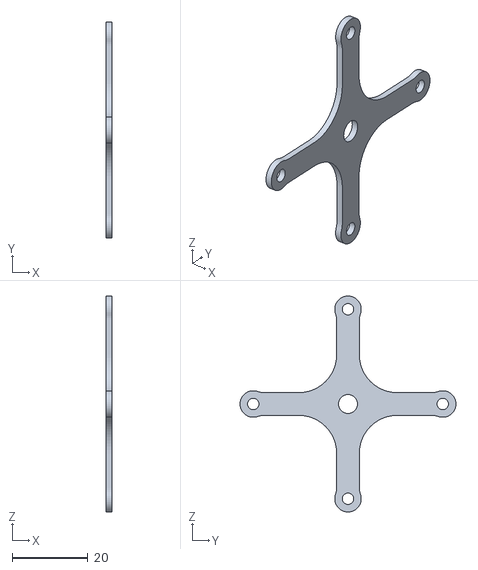
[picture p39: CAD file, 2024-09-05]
CATIA_designs/Cyclorotor_Parts/Controlrod wheel.stl
1.50 x 57.0 x 57.0

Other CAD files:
CATIA_designs/Cyclorotor.CATProduct
